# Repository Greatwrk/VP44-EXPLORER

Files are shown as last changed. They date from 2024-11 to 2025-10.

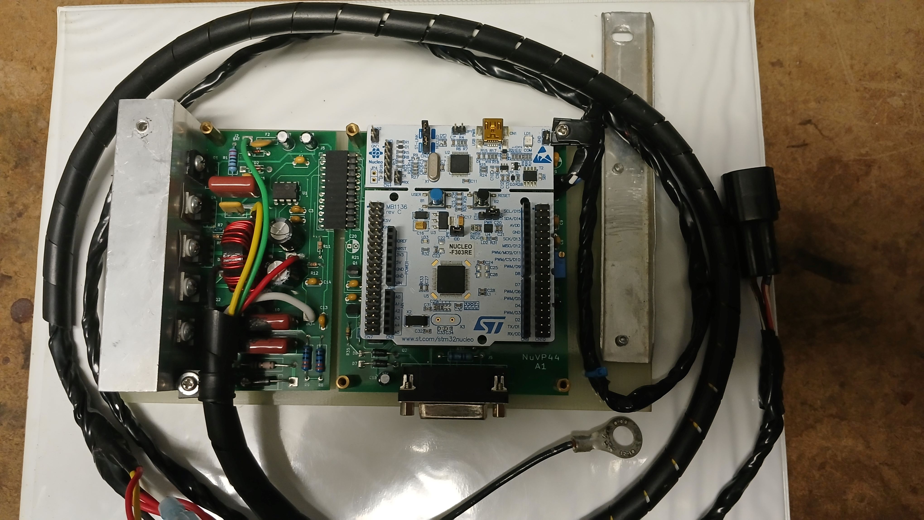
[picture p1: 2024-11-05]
images/VP44 explorer.jpg

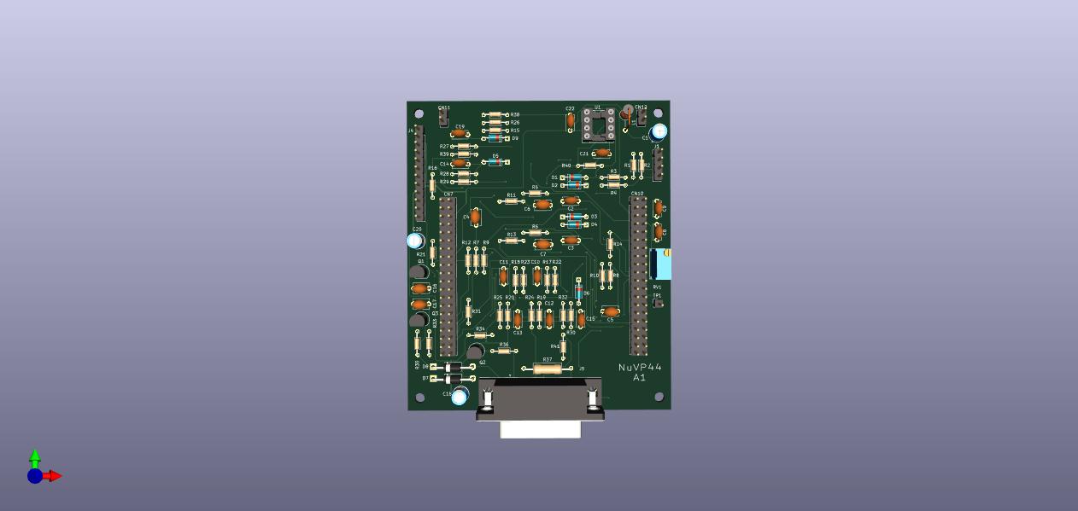
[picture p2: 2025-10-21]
vp44explorer/VP44expMainJ5/VP44expMainJ5.jpg

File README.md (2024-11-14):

# VP44 EXPLORER

My project replaces the control board that sits on top of the pump with a remote board.
The project uses an STM32f303 Nucleo dev. Board and I used Arduino IDE.
A custom PCB was made in two parts. One is the main logic and sensor interface. The second part is the 
solenoid drivers and power supply. The current driver board uses a high-speed switching buck converter
to operate the fuel solenoid. A linear drive board is under development.
The linear method is the OEM style. It generates a lot of heat and is cooled by the fuel flowing
under it in the pump housing. The switching method results in significantly less heat. The downside is the switching signal can
mask the current monitoring of the solenoid. As the armature plunger moves it causes a change in inductance which causes a small current blip.
The blip is useful to determine the solenoid dead time.

The VP44 shaft has a toothed wheel, the tooth spacing is 3 degrees of crankshaft rotation.
Every 60 degrees (120 at crankshaft) is a pair of staggered teeth.
These I refer to as the index tooth.
A dual magneto-resistive sensor with a back bias magnet senses the teeth as they pass by and creates two sinewaves.
The one that leads I refer to as phase A. The second follows by approximately 90 degrees, I refer to it as phase B.
Both signals are adaptive zero crossing detected by internal opAmps and the DACs in the STM32 and then fed to timer captures.
The software detects the index tooth region and resets a tooth edge counter to zero.
On the tooth edge 19 of the B phase the radial injection plungers are at their maximum extension.
As they follow the cam ring into compression it's at this position the injection solenoid valve must be fully transitioned to the closed position.
This is the start of injection SOI. After a variable amount of degrees, the valve de-energizes this is the end of injection EOI.

Since the solenoid has deadtime on both turn on and turn off the switching must occur before edge 19 or EOI actually happens.
This is done by computing shaft position, velocity, and acceleration to predict the relative time from a current tooth edge to edge 19.
Obviously, the closer we are to the edge 19 event the better the prediction will be, but at higher RPMs the deadtime of the solenoid results in the required prediction to
occur many degrees in advance else the valve will be closed too late or early.
That results in late injection, reduced fuel delivery and hazy smoke.
The valve must be de-energized before the moment of desired EOI because of mechanical delay I call this release time, which is about 850 microseconds.
The dead time is mostly dependent on the battery voltage and must be calculated often. 
A full current is applied to get the valve moving then the current is reduced to prevent the valve from slamming on its seat and bouncing.
Finally, the current is reduced to a safe level for the majority of the injection event.
The switch-off induction spike at EOI must be clamped at a higher voltage and low current for a fast release.
The magnetic field is determined largely by A x N turns, so keeping current low speeds the armature release.
Simple clamping / recirculating methods are too slow. A zener diode RC circuit is used. 
Some manual adjustments to times and current values must be determined with an oscilloscope and are stored.

Anyone who has kick-started or rope-started a small engine has experienced the rapid fluctuations that occur in 
crankshaft velocity. These also occur in a running engine but are greatly reduced by the flywheel mass
and inertia. These variations have to be accounted for in both the SOI time and EOI time if not the
engine will start to run rough which makes the variations worse and results in timing and delivery
errors and possible stalling or running away.

The timing advance is determined by the phase relationship of the cam ring to the crankshaft position.
The ECU decodes the crankshaft position sensor and cam sensor to create a reference signal that
occurs at 20 degrees after top dead center for each cylinder. Later engines removed the CKP and changed the camshaft gear. 
With my project, the decoding is done internally and the ECU is not required. 
The cam ring moves by a hydraulic piston which is controlled by another solenoid valve. It is PWM controlled by the MCU. 
The actual timing is calculated by the VP tooth signal phase relationship to the CKP-derived signal. 
A software servo control loop adjusts the PWM to match the computed timing with the desired timing contained in the usual look-up tables.

For now, the TPS, MAP and CKP are all that's required. The CMP is optional. A CAN interface is on the board and a CAN interface is being developed.
The Schematic and PCB were made with KiCad. The code has some low-level stuff for some of the peripherals that at the time were not supported by STM32duino.

If you build this I suggest using a 2 ohm 50 W resistor in place of the fuel solenoid for testing with a scope. The resistor can later be placed
in series with the solenoid to protect it on the bench while sweep testing at RPMs and Fuel levels. Listen for any malfunctions.
The power transistors must be isolated from the heatsink with silicon insulators. Always test isolation with an DVM.

# See it run [HERE](https://www.youtube.com/watch?v=DHwnkv7ZLJk)

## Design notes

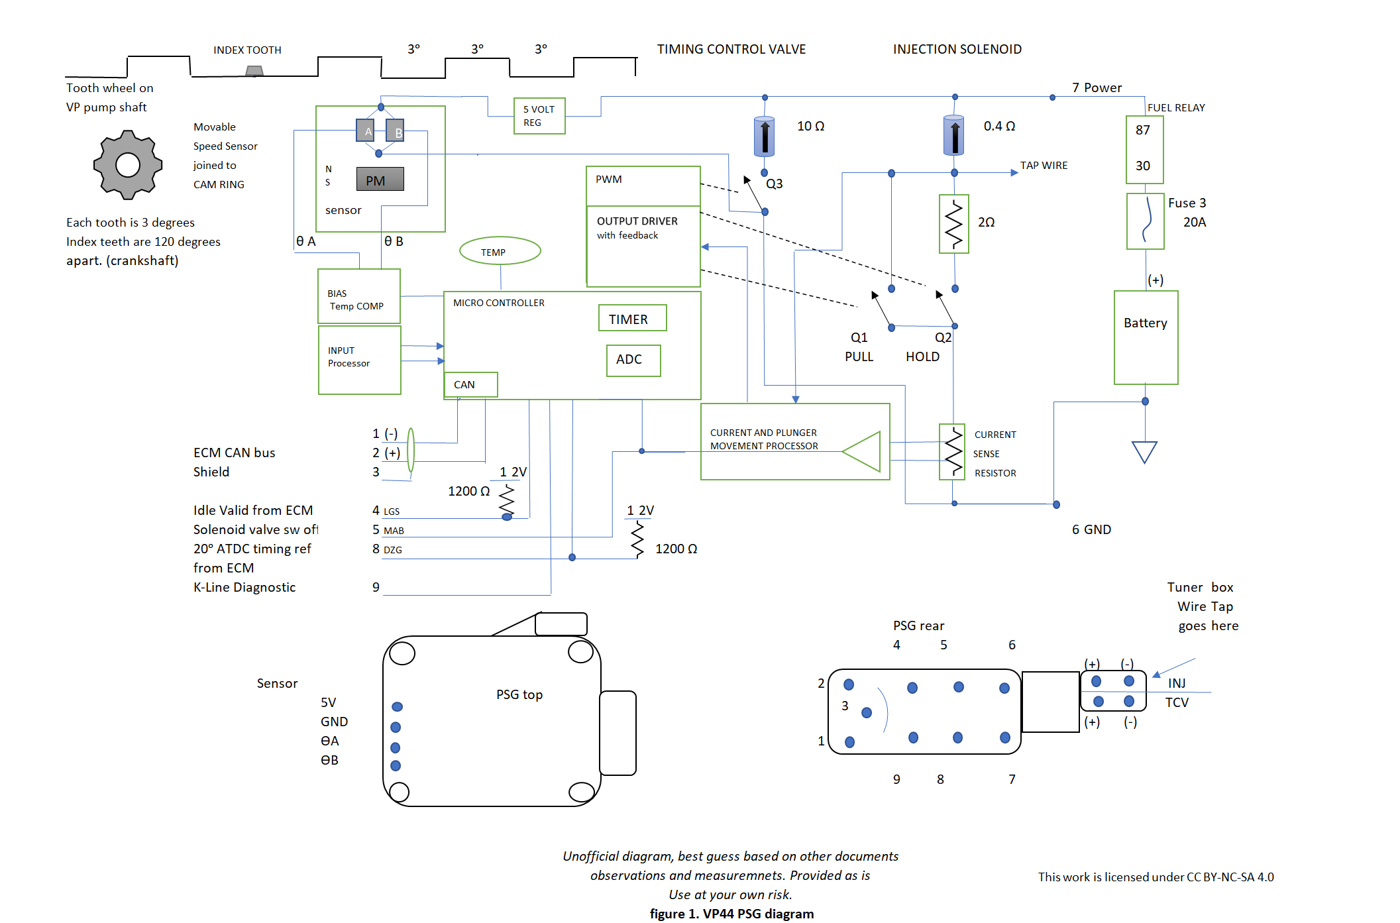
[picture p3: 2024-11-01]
images/Vp block diagram.png

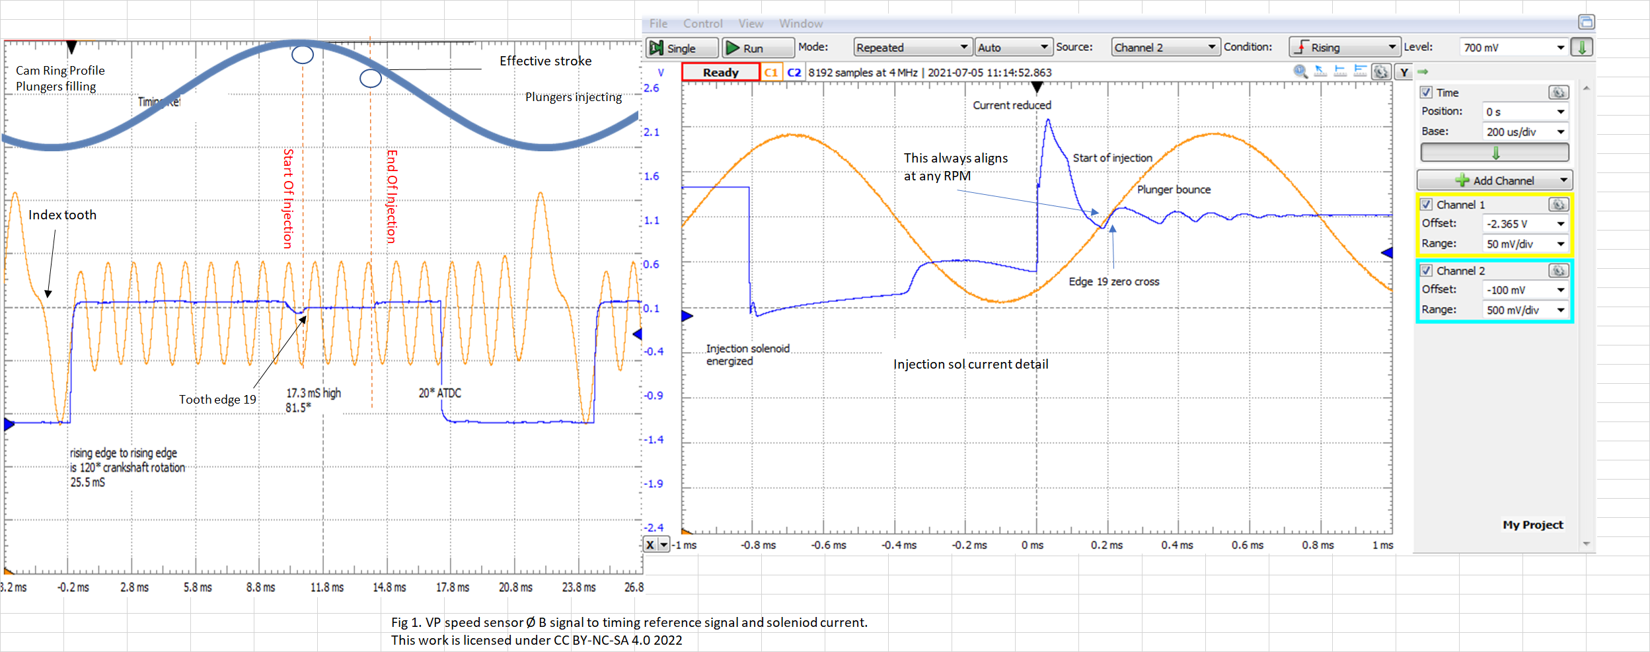
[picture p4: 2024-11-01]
images/vp roller.png

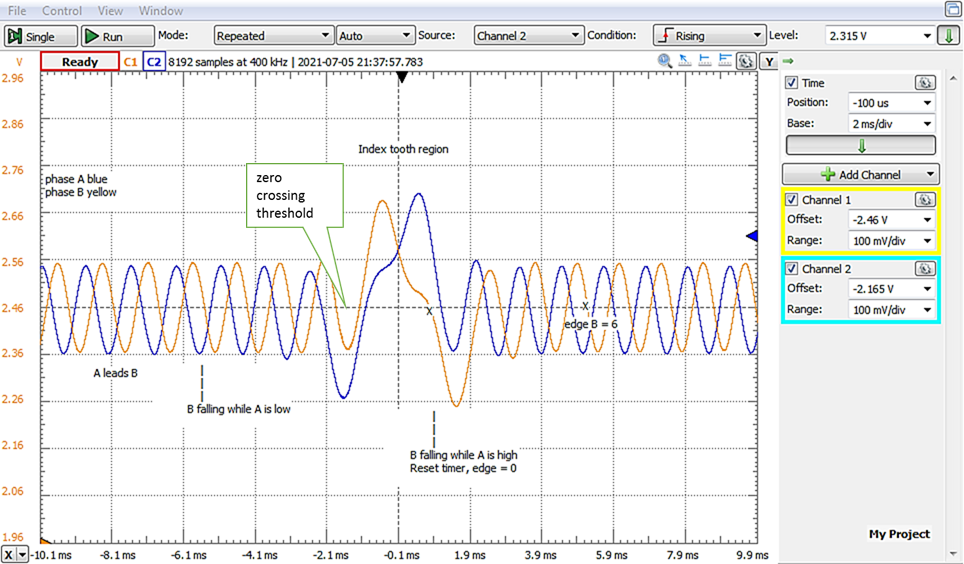
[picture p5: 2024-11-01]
images/VP44 sensor.png

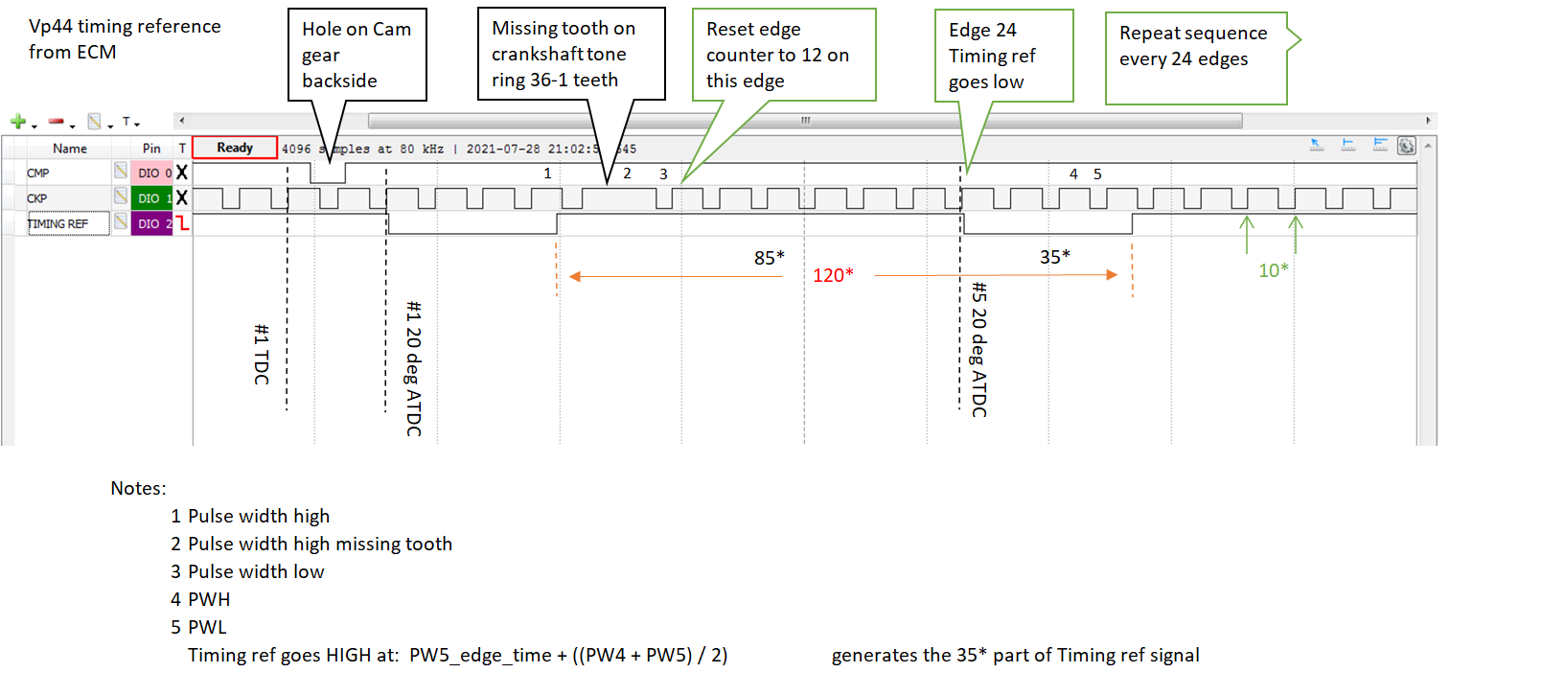
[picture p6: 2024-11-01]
images/TrefECM.png

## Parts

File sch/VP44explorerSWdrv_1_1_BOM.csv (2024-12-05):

Reference | Value | Footprint | Datasheet | Field4 | Sim.Device | Sim.Pins | Sim.Type | Qty
C1, C4, C5 | 1uF | Capacitor_THT:C_Disc_D5.1mm_W3.2mm_P5.00mm | ~ |  |  |  |  | 3
C2, C8 | 100uF | Capacitor_THT:CP_Radial_D5.0mm_P2.50mm | ~ |  |  |  |  | 2
C3, C13, C14 | 0.1uF | Capacitor_THT:C_Disc_D5.0mm_W2.5mm_P5.00mm | ~ |  |  |  |  | 3
C6, C7 | 470uF | Capacitor_THT:CP_Radial_D8.0mm_P5.00mm | ~ |  |  |  |  | 2
C9-C12 | 1uF | Capacitor_THT:C_Rect_L16.5mm_W7.0mm_P15.00mm_MKT | DigiKey EF2105-ND, MFR# ECQ-E2105KF hi quality film cap only |  |  |  |  | 4
D1 | 1N914B | Diode_THT:D_DO-35_SOD27_P7.62mm_Horizontal | ~ |  | D | 1=K 2=A |  | 1
D2 | 5.6V | Diode_THT:D_DO-41_SOD81_P10.16mm_Horizontal | ~ |  |  |  |  | 1
D3 | STPS20H100CT | Package_TO_SOT_THT:TO-220-3_Vertical | ~ |  |  |  |  | 1
D4 | 39V_5W | Diode_THT:D_DO-201AD_P15.24mm_Horizontal | ~ |  |  |  |  | 1
F1 | 20A | Automotive ATC | ~ |  |  |  |  | 1
F2 | Polyfuse 1A | Capacitor_THT:C_Disc_D8.0mm_W2.5mm_P5.00mm | MF-RHT 100-2CT-ND PTC 30V IA |  |  |  |  | 1
F3 | Polyfuse 2.5A | Capacitor_THT:C_Disc_D8.0mm_W2.5mm_P5.00mm | LITTLE FUSE POLY SWITCH 2.5A |  |  |  |  | 1
HS1 | Heatsink | 100 X 40 X20 AMAZON.COM | ~ |  |  |  |  | 1
J1 | GND | Connector_Wire:SolderWire-2sqmm_1x01_D2mm_OD3.9mm | ~ |  |  |  |  | 1
J2 | BAT | Connector_Wire:SolderWire-2sqmm_1x01_D2mm_OD3.9mm | ~ |  |  |  |  | 1
J3 | TCV | Connector_Wire:SolderWire-2sqmm_1x01_D2mm_OD3.9mm | ~ |  |  |  |  | 1
J4 | INJ+ | Connector_Wire:SolderWire-2sqmm_1x01_D2mm_OD3.9mm | ~ |  |  |  |  | 1
J5 | Conn_01x12 | Connector_PinHeader_2.54mm:PinHeader_1x12_P2.54mm_Right angle female | ~ S5448-ND |  |  |  |  | 1
J6 | INJ | Connector_Wire:SolderWire-2sqmm_1x01_D2mm_OD3.9mm | ~ | INJ- |  |  |  | 1
L1 | L_Ferrite | Inductor_THT:L_Toroid_Vertical_L26.7mm_W14.0mm_P10.16mm_Pulse_D | Amazon.com DC 300W 20A step down buck converter, re used coil |  |  |  |  | 1
L2 | TCV_SOL |  | ~ |  |  |  |  | 1
L3 | INJ_SOL |  | ~ |  |  |  |  | 1
Q1 | MJF44H11G | Package_TO_SOT_THT:TO-220-3_Vertical | https://www.onsemi.com/pub/Collateral/BDW93C-D.pdf |  |  |  |  | 1
Q2 | IRF135B203 | Package_TO_SOT_THT:TO-220-3_Vertical | https://www.st.com/resource/en/datasheet/stp40n60m2.pdf |  | NMOS | 1=D 2=G 3=S | VDMOS | 1
Q3, Q4 | STP40NF10L | Package_TO_SOT_THT:TO-220-3_Vertical | https://www.st.com/resource/en/datasheet/stp40n60m2.pdf |  | NMOS | 1=D 2=G 3=S | VDMOS | 2
R1 | 220R | Resistor_THT:R_Axial_DIN0309_L9.0mm_D3.2mm_P15.24mm_Horizontal | ~ |  |  |  |  | 1
R2, R4 | 27R | Resistor_THT:R_Axial_DIN0204_L3.6mm_D1.6mm_P7.62mm_Horizontal | ~ |  |  |  |  | 2
R3, R5, R8, R11-R14 | 10K | Resistor_THT:R_Axial_DIN0204_L3.6mm_D1.6mm_P7.62mm_Horizontal | ~ |  |  |  |  | 7
R6, R9 | 330R | Resistor_THT:R_Axial_DIN0309_L9.0mm_D3.2mm_P15.24mm_Horizontal | ~ |  |  |  |  | 2
R7 | 100R | Resistor_THT:R_Axial_DIN0204_L3.6mm_D1.6mm_P7.62mm_Horizontal | ~ |  |  |  |  | 1
R10 | 1R_1W | Resistor_THT:R_Axial_DIN0414_L11.9mm_D4.5mm_P20.32mm_Horizontal | ~ |  |  |  |  | 1
U1 | MCP14E7 | Package_DIP:DIP-8_W7.62mm | http://ww1.microchip.com/downloads/en/DeviceDoc/MCP14E7.pdf |  |  |  |  | 1
U2 | ACS712xLCTR-20A | Package_SO:SOIC-8_3.9x4.9mm_P1.27mm | http://www.allegromicro.com/~/media/Files/Datasheets/ACS712-Datasheet.ashx?la=en |  |  |  |  | 1

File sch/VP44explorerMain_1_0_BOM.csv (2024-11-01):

Reference | Value | Footprint | Datasheet | Qty
C1, C18, C20 | 100uF | Capacitor_THT:CP_Radial_D5.0mm_P2.50mm | ~ | 3
C2, C3 | 4.7nF | Capacitor_THT:C_Disc_D5.0mm_W2.5mm_P5.00mm | ~ | 2
C4-C7, C16, C17 | 1uF | Capacitor_THT:C_Disc_D5.1mm_W3.2mm_P5.00mm | ~ | 6
C8, C12, C13 | 300pF | Capacitor_THT:C_Disc_D5.0mm_W2.5mm_P5.00mm | ~ | 3
C9, C19 | 10nF | Capacitor_THT:C_Disc_D5.0mm_W2.5mm_P5.00mm | ~ | 2
C10, C11, C14, C15, C21, C22 | 0.1uF | Capacitor_THT:C_Disc_D5.0mm_W2.5mm_P5.00mm | ~ | 6
CN7, CN10 | Conn_02x20_Odd_Even | Connector_PinHeader_2.54mm:PinHeader_2x20_P2.54mm_Vertical | ~ | 2
CN11, CN12 | Conn_01x02_Female | Connector_PinHeader_2.54mm:PinHeader_1x02_P2.54mm_Vertical | ~ | 2
D1-D6, D9 | 1N914B | Diode_THT:D_DO-35_SOD27_P7.62mm_Horizontal | ~ | 7
D7, D8 | 1N5393 | Diode_THT:D_DO-41_SOD81_P12.70mm_Horizontal | ~ | 2
J1 | Conn_01x04_Shielded | Connector_PinHeader_2.54mm:PinHeader_1x04_P2.54mm_Vertical | ~ | 1
J4 | Conn_01x12 | Connector_PinHeader_2.54mm:PinHeader_1x12_P2.54mm_Vertical | ~ | 1
J5 | DB15_Male_MountingHoles | Connector_Dsub:DSUB-15_Male_Horizontal_P2.77x2.84mm_EdgePinOffset4.94mm_Housed_MountingHolesOffset7.48mm | digikey 182-15FE-ND , MFR 182-015-213R531 | 1
L1 | 500uH | Inductor_THT:L_Axial_L11.0mm_D4.5mm_P5.08mm_Vertical_Fastron_MECC | ~ | 1
Q1, Q2 | PN2222A | Package_TO_SOT_THT:TO-92_Inline | http://www.fairchildsemi.com/ds/PN/PN2222A.pdf | 2
Q3 | BC327 | Package_TO_SOT_THT:TO-92_Inline | http://www.onsemi.com/pub_link/Collateral/BC327-D.PDF | 1
R1-R4, R7, R8, R31, R41 | 1.5K | Resistor_THT:R_Axial_DIN0204_L3.6mm_D1.6mm_P7.62mm_Horizontal | ~ | 8
R5, R6, R26 | 47K | Resistor_THT:R_Axial_DIN0204_L3.6mm_D1.6mm_P7.62mm_Horizontal | ~ | 3
R9, R10 | 470K | Resistor_THT:R_Axial_DIN0204_L3.6mm_D1.6mm_P7.62mm_Horizontal | ~ | 2
R11, R13, R15 | 1K | Resistor_THT:R_Axial_DIN0204_L3.6mm_D1.6mm_P7.62mm_Horizontal | ~ | 3
R12, R14, R17-R20, R22-R25, R30, R32, R34, R39 | 10K | Resistor_THT:R_Axial_DIN0204_L3.6mm_D1.6mm_P7.62mm_Horizontal | ~ | 14
R16, R27, R33 | 4.7K | Resistor_THT:R_Axial_DIN0204_L3.6mm_D1.6mm_P7.62mm_Horizontal | ~ | 3
R21 | 2.2K | Resistor_THT:R_Axial_DIN0204_L3.6mm_D1.6mm_P7.62mm_Horizontal | ~ | 1
R28 | 3.9K | Resistor_THT:R_Axial_DIN0204_L3.6mm_D1.6mm_P7.62mm_Horizontal | ~ | 1
R29 | 15K | Resistor_THT:R_Axial_DIN0204_L3.6mm_D1.6mm_P7.62mm_Horizontal | ~ | 1
R35 | 100K | Resistor_THT:R_Axial_DIN0204_L3.6mm_D1.6mm_P7.62mm_Horizontal | ~ | 1
R36 | 33R | Resistor_THT:R_Axial_DIN0204_L3.6mm_D1.6mm_P7.62mm_Horizontal | ~ | 1
R37 | 4.7R_1/2W | Resistor_THT:R_Axial_DIN0309_L9.0mm_D3.2mm_P15.24mm_Horizontal | ~ | 1
R38 | 2K | Resistor_THT:R_Axial_DIN0204_L3.6mm_D1.6mm_P7.62mm_Horizontal | ~ | 1
R40 | 120R | Resistor_THT:R_Axial_DIN0204_L3.6mm_D1.6mm_P7.62mm_Horizontal | ~ | 1
RV1 | 100K | Potentiometer_THT:Potentiometer_Bourns_3296W_Vertical | ~ | 1
TP1 | Conn_01x01_Male | Connector_PinHeader_2.54mm:PinHeader_1x01_P2.54mm_Vertical | ~ | 1
U1 | MCP2562-E-P | Package_DIP:DIP-8_W7.62mm_Socket | http://ww1.microchip.com/downloads/en/DeviceDoc/25167A.pdf | 1

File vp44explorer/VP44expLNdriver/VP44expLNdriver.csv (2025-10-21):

Source: | C:\Users\Marcus\Desktop\PCroll\032523nudrvsw\041723nudrln\041723nudrln.kicad_sch
Date: | 4/29/2023 2:43:34 PM
Tool: | Eeschema (7.0.0)
Generator: | C:\Program Files\KiCad\7.0\bin\scripting\plugins/bom_csv_grouped_by_value_with_fp.py
Component Count: | 43
Ref | Qnty | Value | Cmp name | Footprint | Description | Vendor | DNP
C1, C4 | 2 | 1uF | C | Capacitor_THT:C_Disc_D5.1mm_W3.2mm_P5.00mm | Unpolarized capacitor
C2, C6 | 2 | 0.1uF | C | Capacitor_THT:C_Disc_D5.1mm_W3.2mm_P5.00mm | Unpolarized capacitor
C3, C7 | 2 | 100uF | C_Polarized_US | Capacitor_THT:CP_Radial_D5.0mm_P2.50mm | Polarized capacitor, US symbol
C5 | 1 | 100pF | C | Capacitor_THT:C_Disc_D5.1mm_W3.2mm_P5.00mm | Unpolarized capacitor
C8 | 1 | 1uF | C | Capacitor_THT:C_Rect_L16.5mm_W7.0mm_P15.00mm_MKT | Unpolarized capacitor
C9 | 1 | 0.1uF | C | Capacitor_THT:C_Rect_L16.5mm_W7.0mm_P15.00mm_MKT | Unpolarized capacitor
D1 | 1 | 1N914B | D | Diode_THT:D_DO-35_SOD27_P7.62mm_Horizontal | Diode
D2 | 1 | 5.6V | D_Zener | Diode_THT:D_DO-41_SOD81_P10.16mm_Horizontal | Zener diode
D3, D4 | 2 | 31V | D_Zener | MYfootprints:D_DO-201AD_P17.78mm_Horizontal | Zener diode
F2, F3 | 2 | Polyfuse | Polyfuse | Capacitor_THT:C_Disc_D8.0mm_W2.5mm_P5.00mm | Resettable fuse, polymeric positive temperature coefficient
J1 | 1 | GND | Conn_01x01_Pin_3 | Connector_Wire:SolderWire-2sqmm_1x01_D2mm_OD3.9mm | Generic connector, single row, 01x01, script generated
J2 | 1 | BAT+ | Conn_01x01_Pin_4 | Connector_Wire:SolderWire-2sqmm_1x01_D2mm_OD3.9mm | Generic connector, single row, 01x01, script generated
J3 | 1 | Conn_01x12 | Conn_01x12 | Connector_PinHeader_2.54mm:PinHeader_1x12_P2.54mm_Vertical | Generic connector, single row, 01x12, script generated (kicad-library-utils/schlib/autogen/connector/)
J4 | 1 | INJ- | Conn_01x01_Pin_1 | Connector_Wire:SolderWire-2sqmm_1x01_D2mm_OD3.9mm | Generic connector, single row, 01x01, script generated
J5 | 1 | TCV- | Conn_01x01_Pin_2 | Connector_Wire:SolderWire-2sqmm_1x01_D2mm_OD3.9mm | Generic connector, single row, 01x01, script generated
J6, J7 | 2 | TCV | Conn_01x01_Pin_2 | Connector_Wire:SolderWire-0.5sqmm_1x01_D0.9mm_OD2.1mm | Generic connector, single row, 01x01, script generated
Q1 | 1 | MJF44H11G | MJE13003 | Package_TO_SOT_THT:TO-220-3_Vertical | 1.5A Ic, 400V Vce, Silicon Switching Power NPN Transistor, TO-225
Q2 | 1 | IRF250P225 | STB40N60M2 | Package_TO_SOT_THT:TO-247-3_Vertical | 34A Id, 600V Vds, N-Channel MDmesh M2 MOSFET, 78mOhm Ron, D2PAK
Q3 | 1 | IRL2910 | STB40N60M2 | Package_TO_SOT_THT:TO-220-3_Vertical | 34A Id, 600V Vds, N-Channel MDmesh M2 MOSFET, 78mOhm Ron, D2PAK
Q4 | 1 | 75NF20 | STB40N60M2 | Package_TO_SOT_THT:TO-220-3_Vertical | 34A Id, 600V Vds, N-Channel MDmesh M2 MOSFET, 78mOhm Ron, D2PAK
R1, R3, R4, R5, R6, R7, R11, R12 | 8 | 10K | R | Resistor_THT:R_Axial_DIN0204_L3.6mm_D1.6mm_P7.62mm_Horizontal | Resistor
R2, R16 | 2 | 220R | R | Resistor_THT:R_Axial_DIN0309_L9.0mm_D3.2mm_P15.24mm_Horizontal | Resistor
R8 | 1 | .05R | R | Resistor_THT:R_Axial_DIN0516_L15.5mm_D5.0mm_P25.40mm_Horizontal | Resistor
R9, R13 | 2 | 100R | R | Resistor_THT:R_Axial_DIN0204_L3.6mm_D1.6mm_P5.08mm_Horizontal | Resistor
R10 | 1 | 100R | R | Resistor_THT:R_Axial_DIN0204_L3.6mm_D1.6mm_P7.62mm_Horizontal | Resistor
R14, R15 | 2 | 1R | R | Package_TO_SOT_THT:TO-220-2_Vertical | Resistor
U1 | 1 | Opamp_Quad | Opamp_Quad | Package_DIP:DIP-14_W7.62mm_Socket | Quad operational amplifier

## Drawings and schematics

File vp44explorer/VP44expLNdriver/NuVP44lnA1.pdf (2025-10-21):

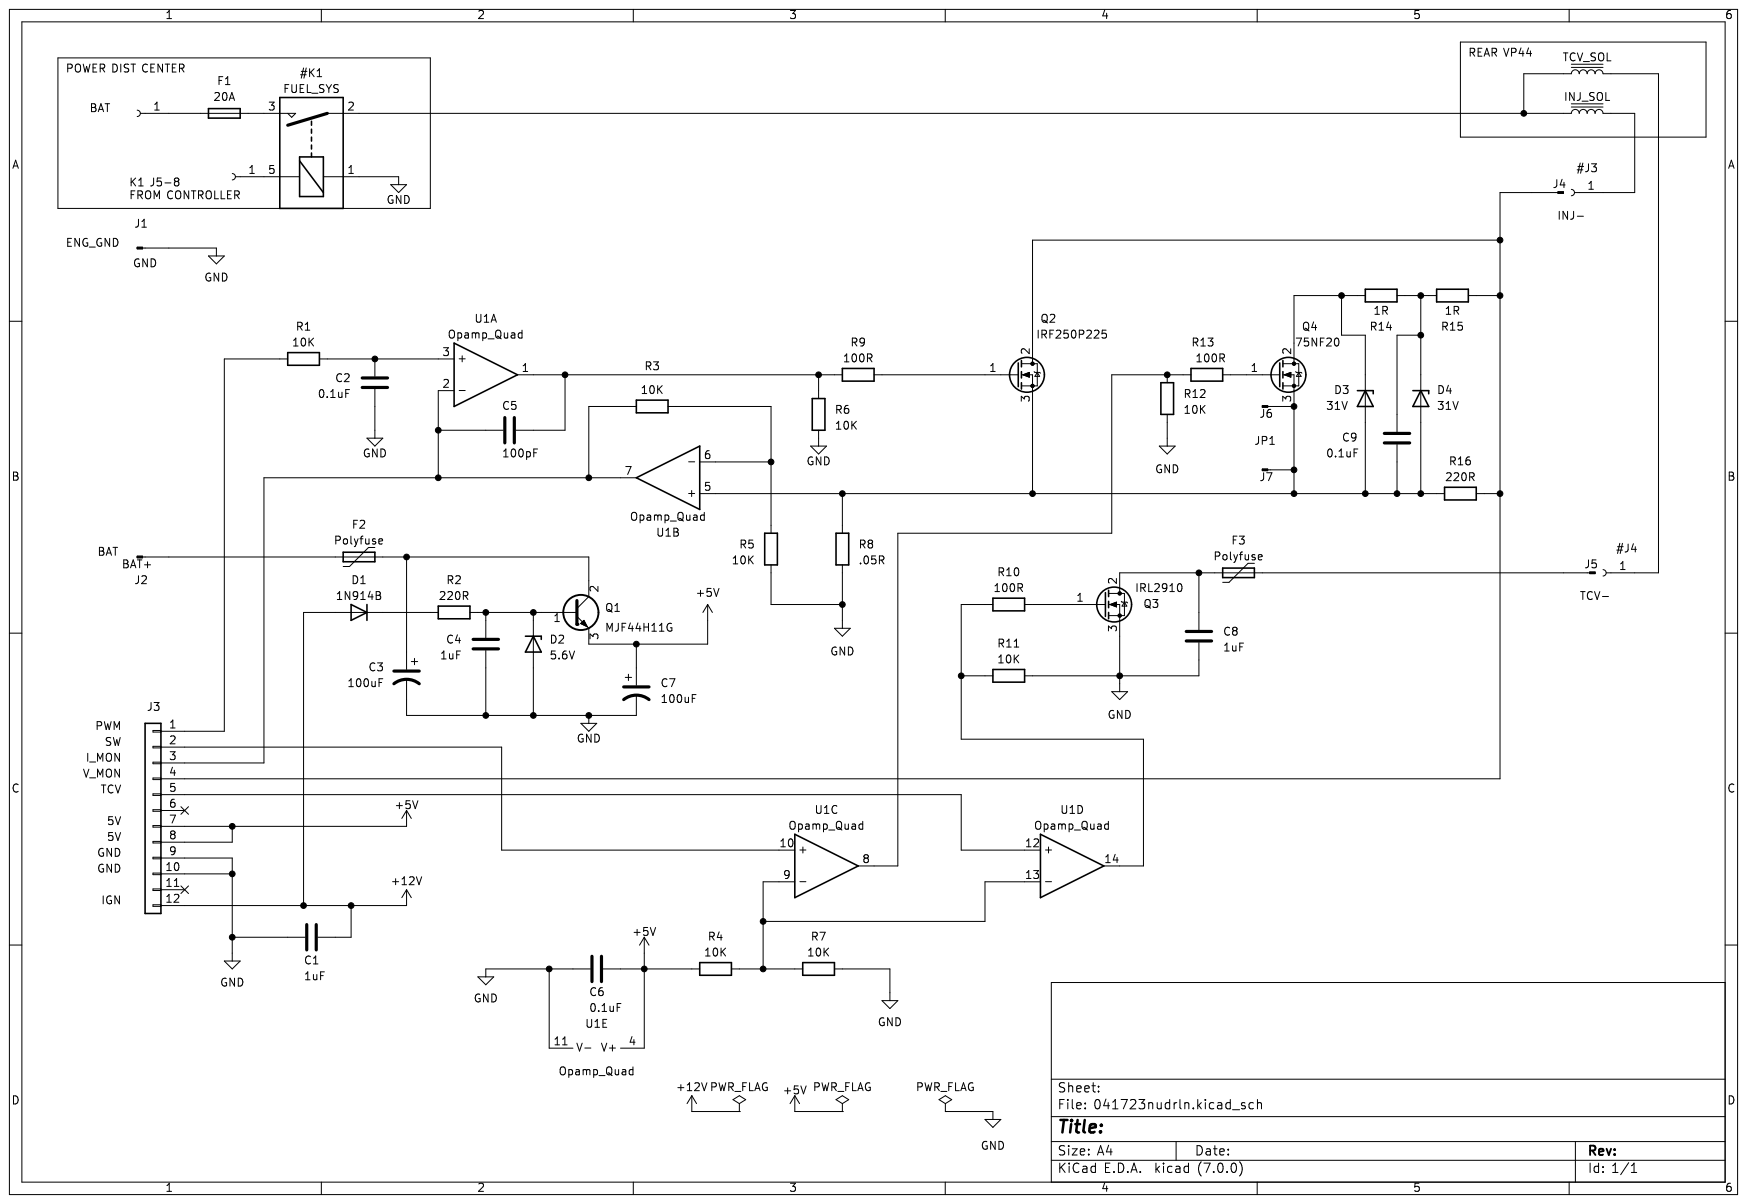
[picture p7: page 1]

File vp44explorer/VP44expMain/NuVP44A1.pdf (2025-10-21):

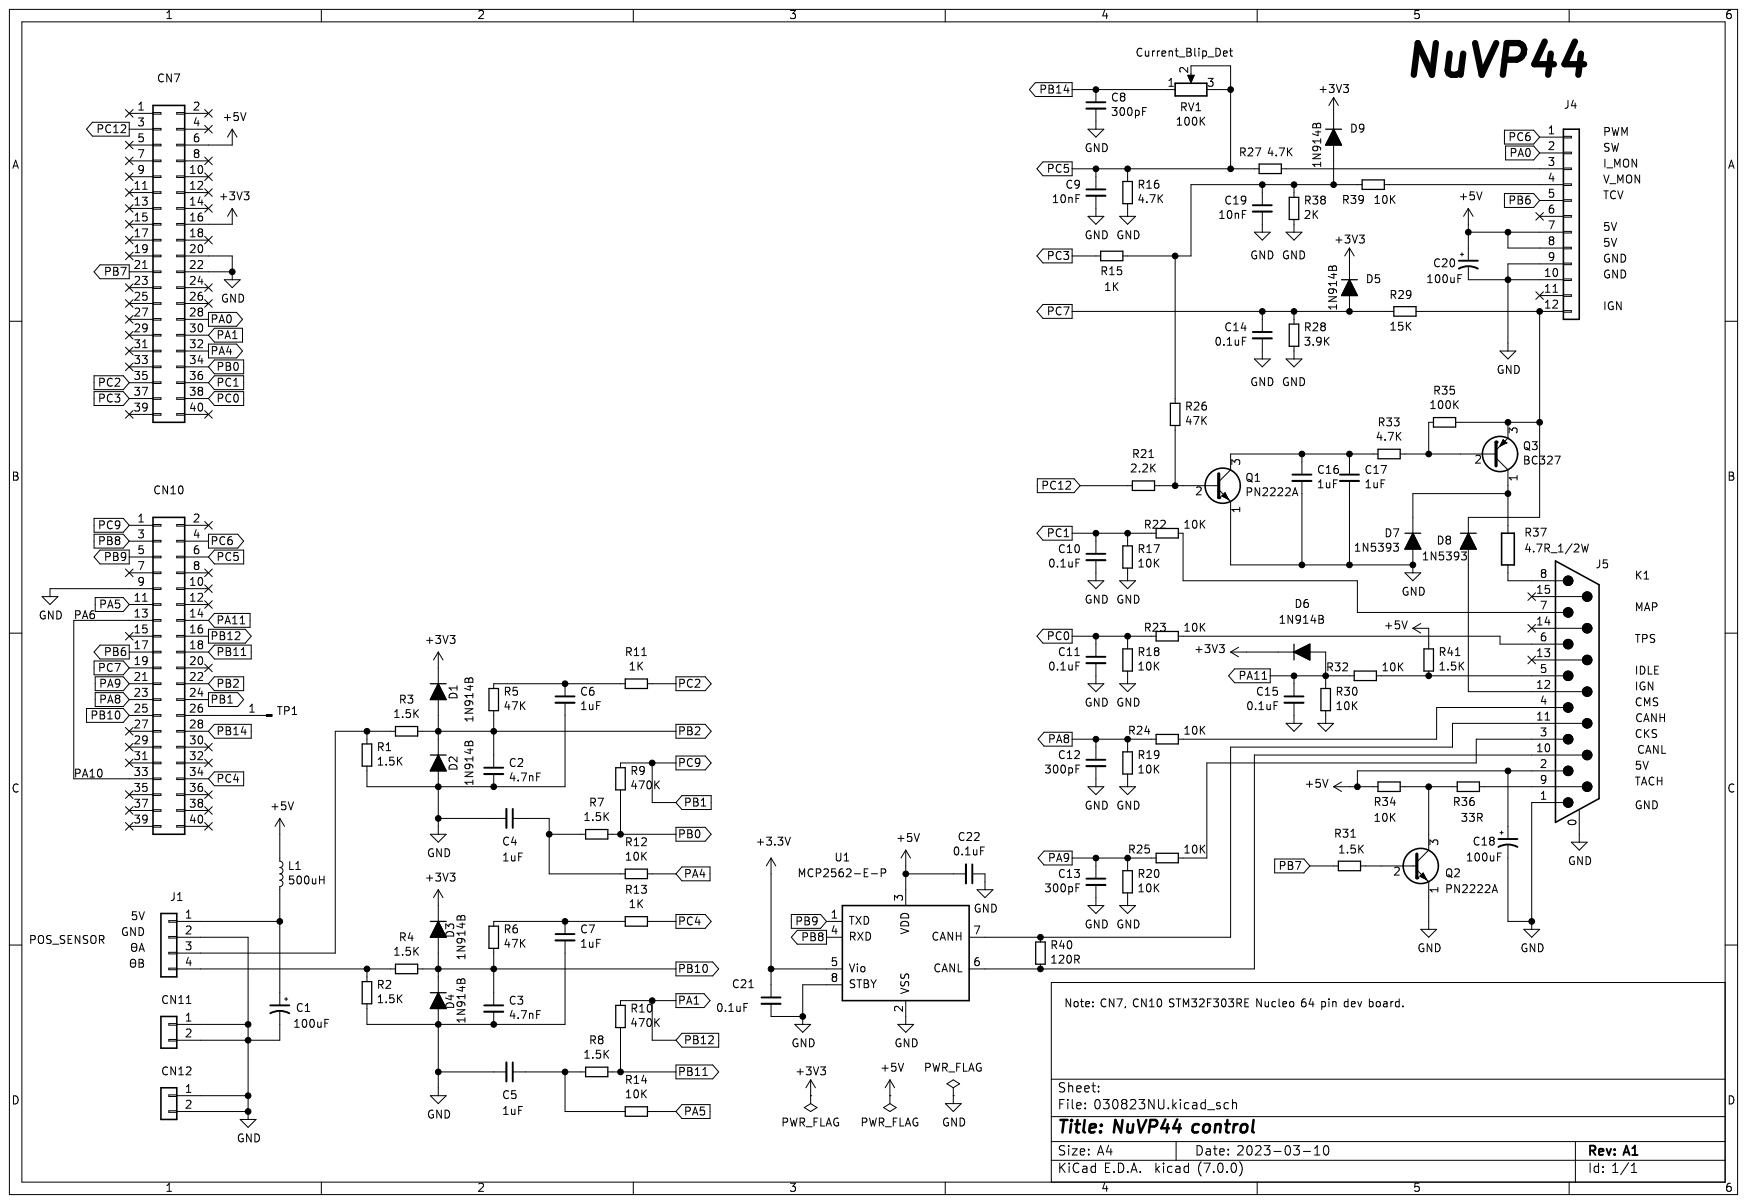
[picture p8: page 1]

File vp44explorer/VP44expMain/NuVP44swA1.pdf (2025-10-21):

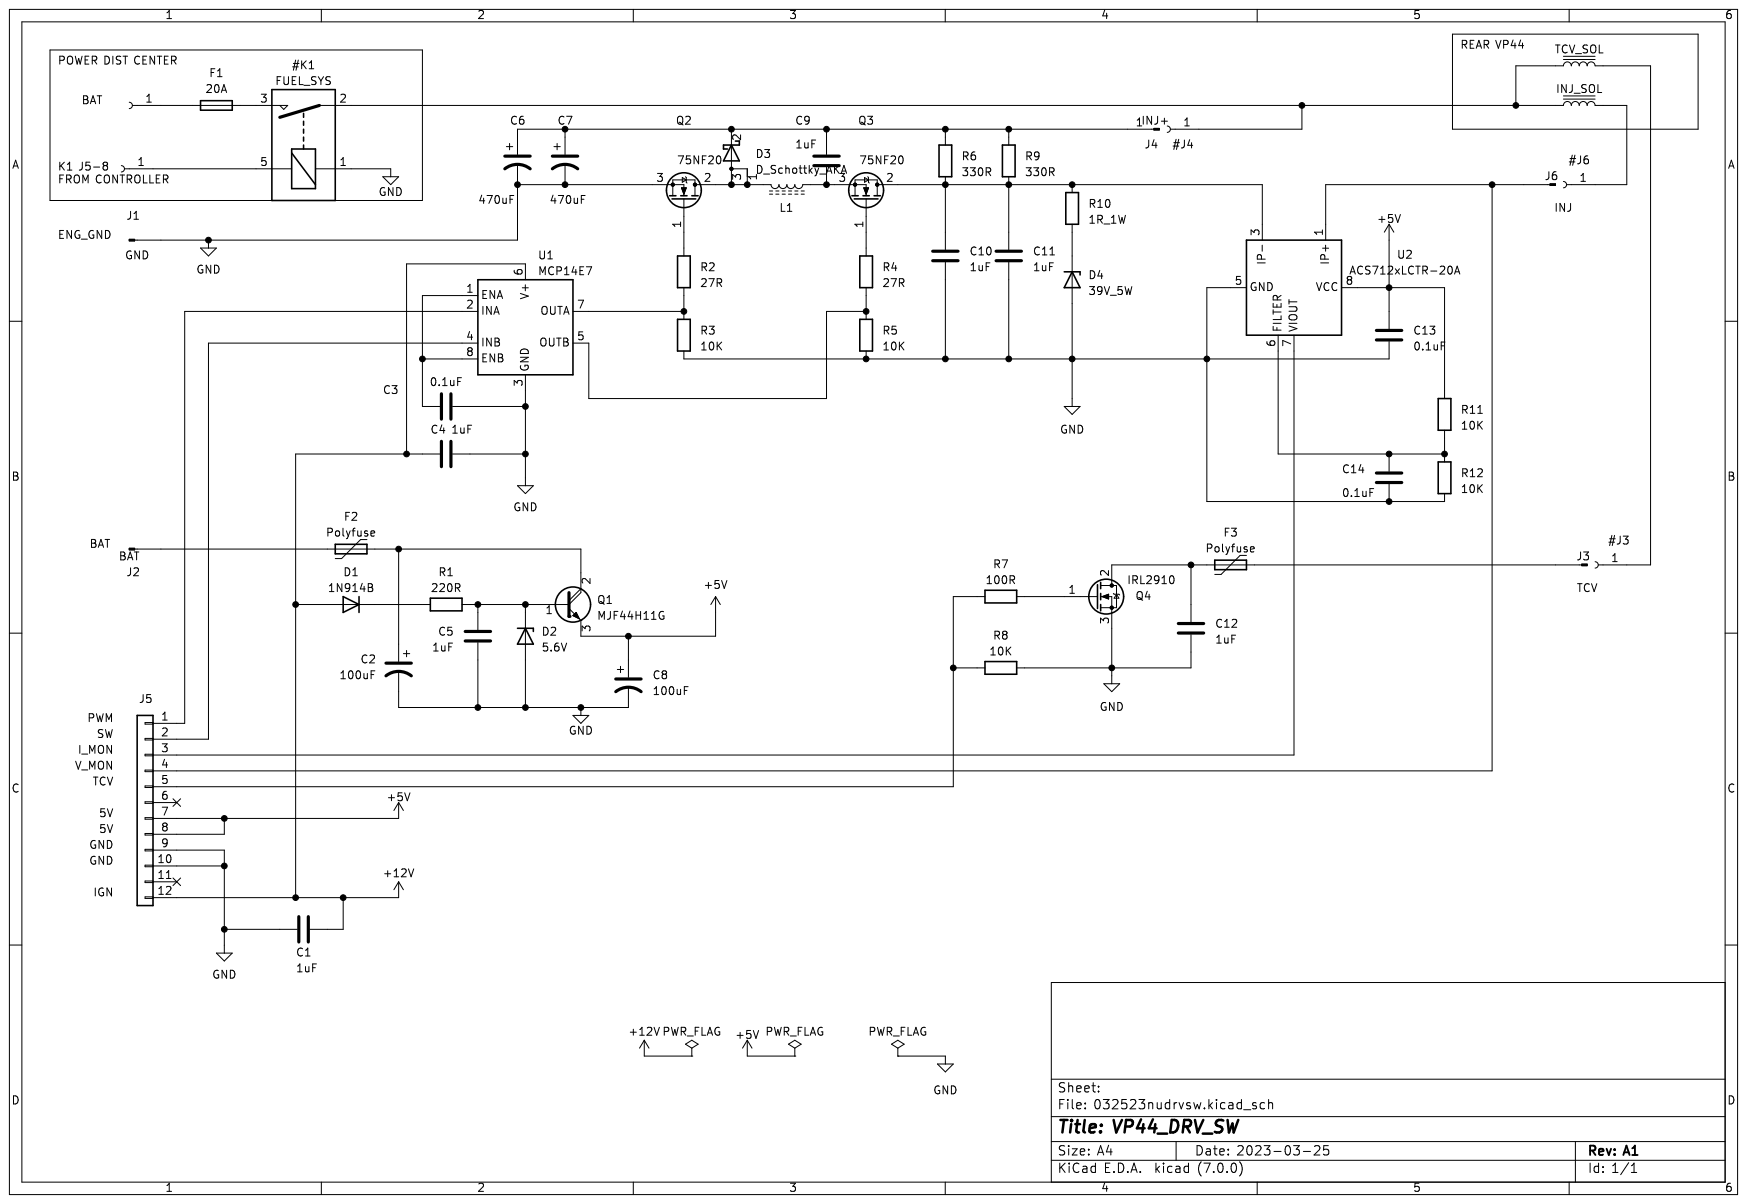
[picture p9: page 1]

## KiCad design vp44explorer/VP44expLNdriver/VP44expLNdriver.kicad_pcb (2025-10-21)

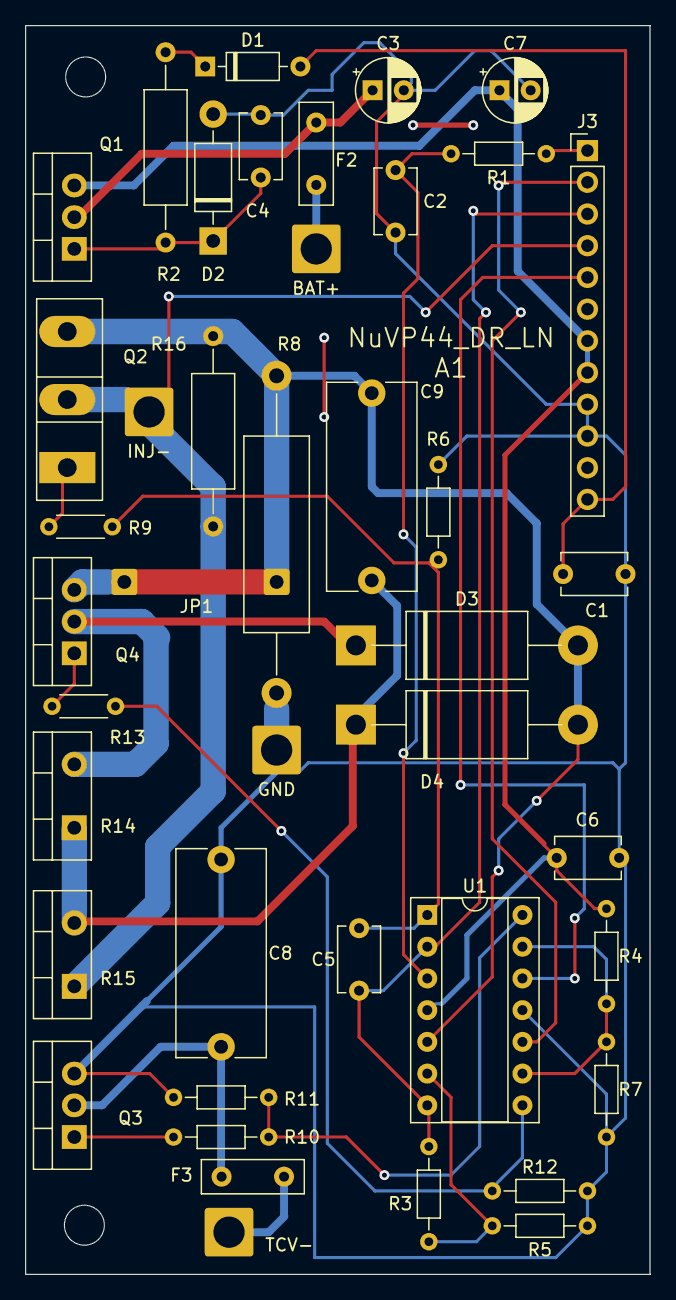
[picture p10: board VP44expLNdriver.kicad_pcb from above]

Board: 2 copper layers, 50.0 x 100.0 mm, 45 parts (0 on the bottom side), 26 nets.

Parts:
C1, C4: 1uF; C_Disc_D5.1mm_W3.2mm_P5.00mm
C2, C6: 0.1uF; C_Disc_D5.1mm_W3.2mm_P5.00mm
C3, C7: 100uF; CP_Radial_D5.0mm_P2.50mm
C5: 100pF; C_Disc_D5.1mm_W3.2mm_P5.00mm
C8: 1uF; C_Rect_L16.5mm_W7.0mm_P15.00mm_MKT
C9: 0.1uF; C_Rect_L16.5mm_W7.0mm_P15.00mm_MKT
D1: 1N914B; D_DO-35_SOD27_P7.62mm_Horizontal
D2: 5.6V; D_DO-41_SOD81_P10.16mm_Horizontal
D3, D4: 31V; D_DO-201AD_P17.78mm_Horizontal
F2, F3: Polyfuse; C_Disc_D8.0mm_W2.5mm_P5.00mm
J1: GND; SolderWire-2sqmm_1x01_D2mm_OD3.9mm
J2: BAT+; SolderWire-2sqmm_1x01_D2mm_OD3.9mm
J3: Conn_01x12; PinHeader_1x12_P2.54mm_Vertical
J4: INJ-; SolderWire-2sqmm_1x01_D2mm_OD3.9mm
J5: TCV-; SolderWire-2sqmm_1x01_D2mm_OD3.9mm
J6, J7: TCV; SolderWire-0.5sqmm_1x01_D0.9mm_OD2.1mm
MH1, MH2: MountingHole_3.2mm_M3
Q1: MJF44H11G; TO-220-3_Vertical
Q2: IRF250P225; TO-247-3_Vertical
Q3: IRL2910; TO-220-3_Vertical
Q4: 75NF20; TO-220-3_Vertical
R1, R3, R4, R5, R6, R7, R11, R12: 10K; R_Axial_DIN0204_L3.6mm_D1.6mm_P7.62mm_Horizontal
R2, R16: 220R; R_Axial_DIN0309_L9.0mm_D3.2mm_P15.24mm_Horizontal
R8: .05R; R_Axial_DIN0516_L15.5mm_D5.0mm_P25.40mm_Horizontal
R9, R13: 100R; R_Axial_DIN0204_L3.6mm_D1.6mm_P5.08mm_Horizontal
R10: 100R; R_Axial_DIN0204_L3.6mm_D1.6mm_P7.62mm_Horizontal
R14, R15: 1R; TO-220-2_Vertical
U1: Opamp_Quad; DIP-14_W7.62mm_Socket

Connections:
+5V: C6.2, C7.1, J3.7, J3.8, Q1.3 (E), R4.1, U1.4 (V+)
+12V: C1.2, D1.2 (A), J3.12
GND: C1.1, C2.1, C3.2, C4.1, C6.1, C7.2, C8.1, D2.2 (A), J1.1, J3.9, J3.10, Q3.3 (S), R5.1, R6.2, R7.2, R8.2, R11.2, R12.2, U1.11 (V-)
unnamed: C5.2, R6.1, R9.1, U1.1
unnamed: D1.1 (K), R2.1
unnamed: C4.2, D2.1 (K), Q1.1 (B), R2.2
unnamed: C9.1, D3.2 (A), D4.2 (A), J6.1, J7.1, Q2.3 (S), Q4.3 (S), R8.1, R16.1, U1.5 (+)
unnamed: D3.1 (K), Q4.2 (D), R14.2
unnamed: C9.2, D4.1 (K), R14.1, R15.2
unnamed: F2.1, J2.1
unnamed: J3.1, R1.1
unnamed: J3.2, U1.10 (+)
unnamed: C5.1, J3.3, R3.1, U1.2 (-), U1.7
unnamed: J3.4, J4.1, Q2.2 (D), R15.1, R16.2
unnamed: J3.5, U1.12 (+)
unnamed: F3.2, J5.1
unnamed: C3.1, F2.2, Q1.2 (C)
unnamed: Q2.1 (G), R9.2
unnamed: C8.2, F3.1, Q3.2 (D)
unnamed: Q3.1 (G), R10.2
unnamed: Q4.1 (G), R13.1
unnamed: R10.1, R11.1, U1.14
unnamed: R12.1, R13.2, U1.8
unnamed: C2.2, R1.2, U1.3 (+)
unnamed: R3.2, R5.2, U1.6 (-)
unnamed: R4.2, R7.1, U1.9 (-), U1.13 (-)

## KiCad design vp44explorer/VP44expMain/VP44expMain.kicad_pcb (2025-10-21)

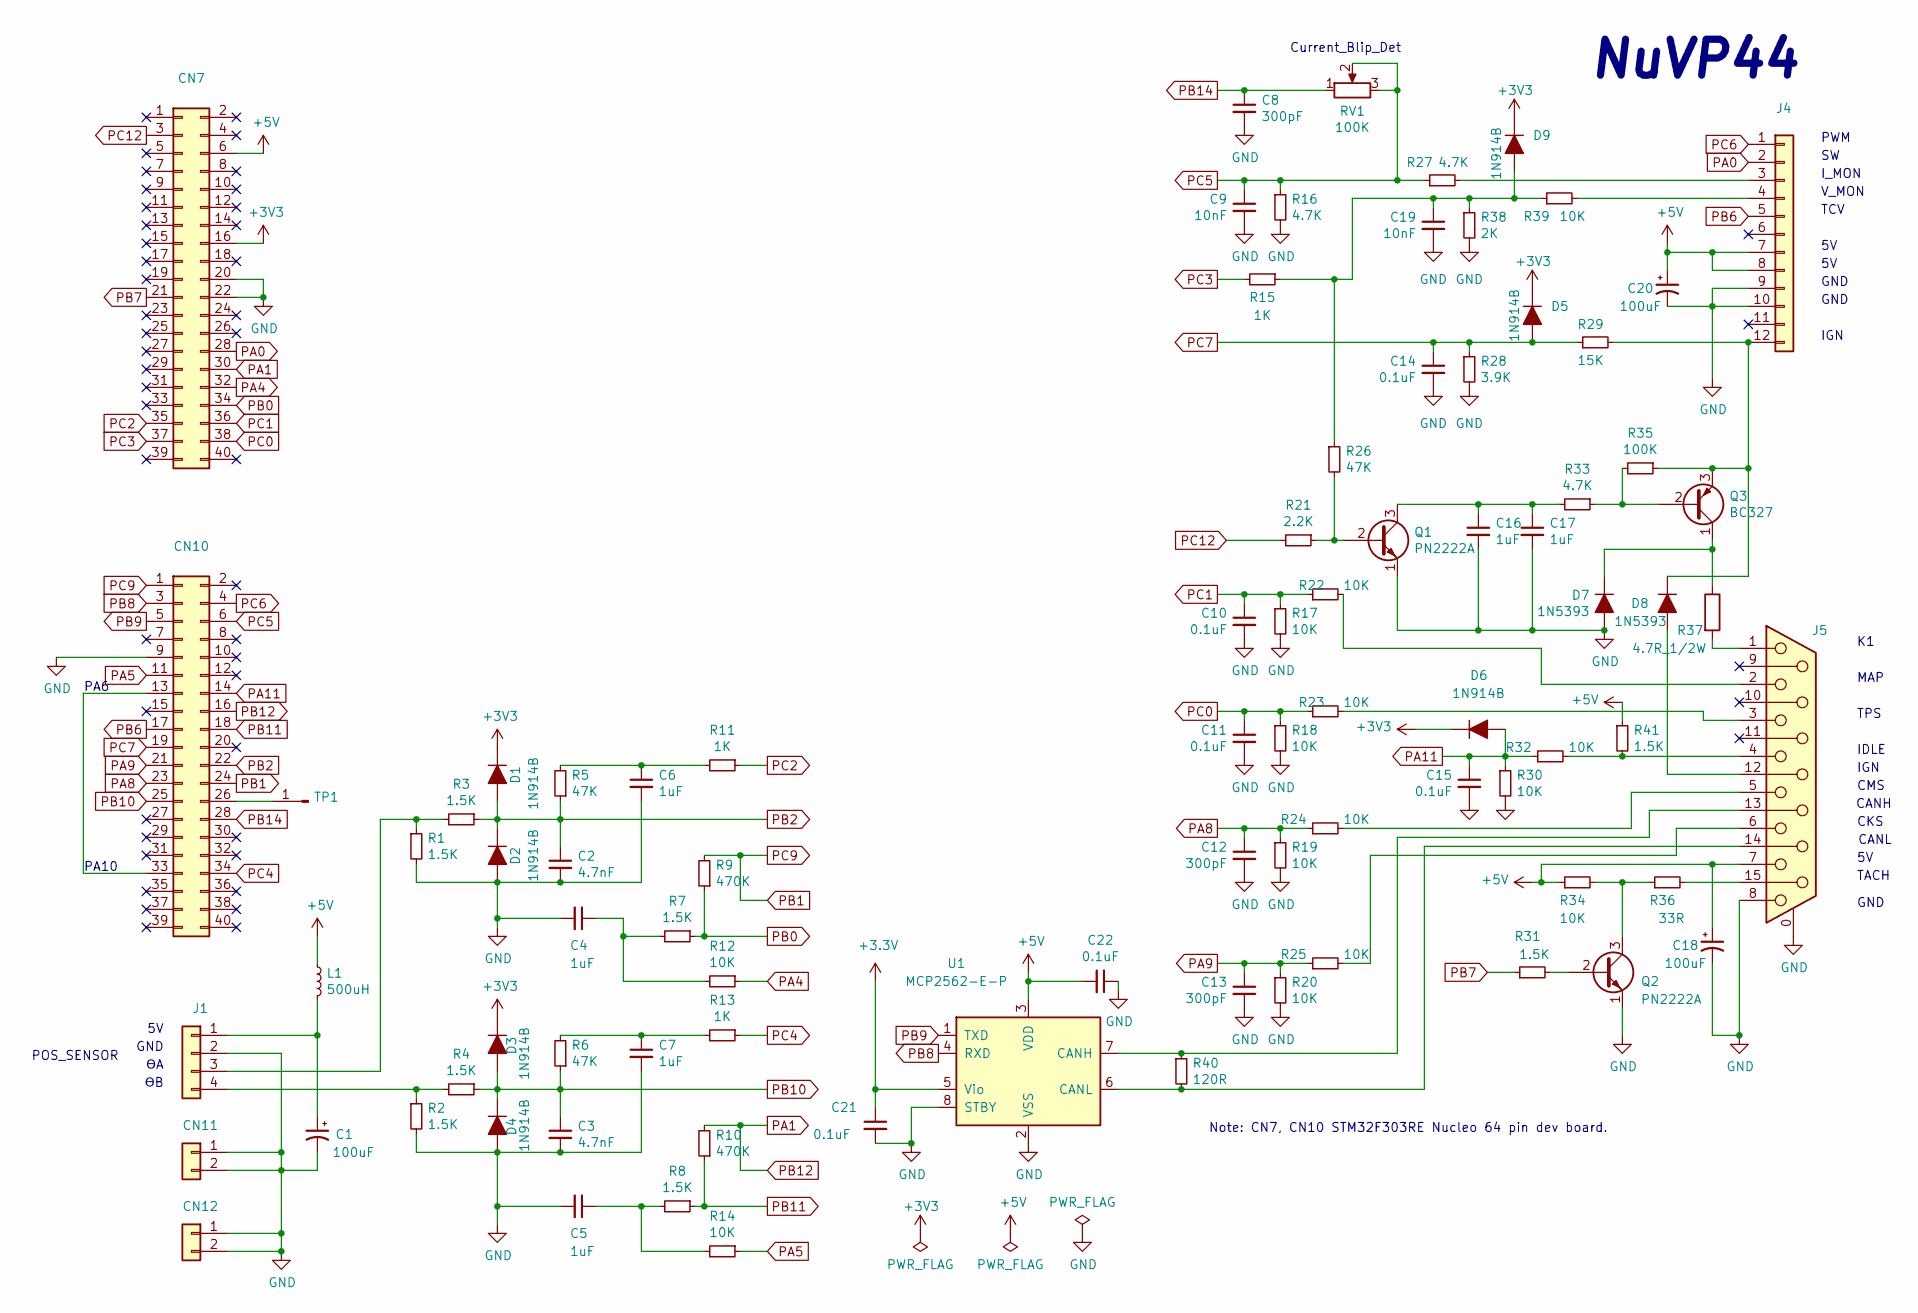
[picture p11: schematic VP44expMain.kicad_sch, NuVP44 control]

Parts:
C1, C18, C20: 100uF; CP_Radial_D5.0mm_P2.50mm
C2, C3: 4.7nF; C_Disc_D5.0mm_W2.5mm_P5.00mm
C4, C5, C6, C7, C16, C17: 1uF; C_Disc_D5.1mm_W3.2mm_P5.00mm
C8, C12, C13: 300pF; C_Disc_D5.0mm_W2.5mm_P5.00mm
C9, C19: 10nF; C_Disc_D5.0mm_W2.5mm_P5.00mm
C10, C11, C14, C15, C21, C22: 0.1uF; C_Disc_D5.0mm_W2.5mm_P5.00mm
CN7, CN10: Conn_02x20_Odd_Even; PinHeader_2x20_P2.54mm_Vertical
CN11, CN12: Conn_01x02_Female; PinHeader_1x02_P2.54mm_Vertical
D1, D2, D3, D4, D5, D6, D9: 1N914B; D_DO-35_SOD27_P7.62mm_Horizontal
D7, D8: 1N5393; D_DO-41_SOD81_P12.70mm_Horizontal
J1: Conn_01x04_Shielded; PinHeader_1x04_P2.54mm_Vertical
J4: Conn_01x12; PinHeader_1x12_P2.54mm_Vertical
J5: DSUB-15_Female_Horizontal_P2.77x2.84mm_EdgePinOffset4.94mm_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
L1: 500uH; L_Axial_L11.0mm_D4.5mm_P5.08mm_Vertical_Fastron_MECC
Q1, Q2: PN2222A; TO-92_Inline
Q3: BC327; TO-92_Inline
R1, R2, R3, R4, R7, R8, R31, R41: 1.5K; R_Axial_DIN0204_L3.6mm_D1.6mm_P7.62mm_Horizontal
R5, R6, R26: 47K; R_Axial_DIN0204_L3.6mm_D1.6mm_P7.62mm_Horizontal
R9, R10: 470K; R_Axial_DIN0204_L3.6mm_D1.6mm_P7.62mm_Horizontal
R11, R13, R15: 1K; R_Axial_DIN0204_L3.6mm_D1.6mm_P7.62mm_Horizontal
R12, R14, R17, R18, R19, R20, R22, R23, R24, R25, R30, R32, R34, R39: 10K; R_Axial_DIN0204_L3.6mm_D1.6mm_P7.62mm_Horizontal
R16, R27, R33: 4.7K; R_Axial_DIN0204_L3.6mm_D1.6mm_P7.62mm_Horizontal
R21: 2.2K; R_Axial_DIN0204_L3.6mm_D1.6mm_P7.62mm_Horizontal
R28: 3.9K; R_Axial_DIN0204_L3.6mm_D1.6mm_P7.62mm_Horizontal
R29: 15K; R_Axial_DIN0204_L3.6mm_D1.6mm_P7.62mm_Horizontal
R35: 100K; R_Axial_DIN0204_L3.6mm_D1.6mm_P7.62mm_Horizontal
R36: 33R; R_Axial_DIN0204_L3.6mm_D1.6mm_P7.62mm_Horizontal
R37: 4.7R_1/2W; R_Axial_DIN0309_L9.0mm_D3.2mm_P15.24mm_Horizontal
R38: 2K; R_Axial_DIN0204_L3.6mm_D1.6mm_P7.62mm_Horizontal
R40: 120R; R_Axial_DIN0204_L3.6mm_D1.6mm_P7.62mm_Horizontal
RV1: 100K; Potentiometer_Bourns_3296W_Vertical
TP1: Conn_01x01_Male; PinHeader_1x01_P2.54mm_Vertical
U1: MCP2562-E-P; DIP-8_W7.62mm_Socket

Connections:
+5V: C18.1, C20.1, C22.2, CN7.6, J4.7, J4.8, J5.7, L1.1, R34.1, R41.1, U1.3 (VDD)
GND: C1.2, C2.2, C3.2, C4.2, C5.2, C6.2, C7.2, C8.2, C9.2, C10.2, C11.2, C12.2, C13.2, C14.2, C15.2, C16.2, C17.2, C18.2, C19.2, C20.2, C21.2, C22.1, CN7.20, CN7.22, CN10.9, CN11.1, CN11.2, CN12.1, CN12.2, D2.2 (A), D4.2 (A), D7.2 (A), J1.2, J4.9, J4.10, J5.0 (PAD), J5.8, Q1.1 (E), Q2.1 (E), R1.2, R2.2, R16.2, R17.2, R18.2, R19.2, R20.2, R28.2, R30.2, R38.2, U1.2 (VSS), U1.8 (STBY)
unnamed: C4.1, R7.2, R12.2
unnamed: C5.1, R8.2, R14.2
unnamed: C6.1, R5.2, R11.2
unnamed: C7.1, R6.2, R13.2
unnamed: CN10.13, CN10.33
unnamed: CN10.26, TP1.1
unnamed: D7.1 (K), Q3.1 (C), R37.1
unnamed: D8.2 (A), J5.12
unnamed: D8.1 (K), J4.12, Q3.3 (E), R29.2, R35.1
unnamed: C19.1, D9.2 (A), R15.1, R26.1, R38.1, R39.1
unnamed: C1.1, J1.1, L1.2
unnamed: J1.3, R1.1, R3.2
unnamed: J1.4, R2.1, R4.2
unnamed: J4.3, R27.2
unnamed: J4.4, R39.2
unnamed: J5.13, R40.1, U1.7 (CANH)
unnamed: J5.14, R40.2, U1.6 (CANL)
unnamed: J5.15, R36.2
unnamed: J5.1, R37.2
unnamed: J5.2, R22.2
unnamed: J5.3, R23.2
unnamed: J5.4, R32.2, R41.2
unnamed: J5.5, R24.2
unnamed: J5.6, R25.2
unnamed: Q1.2 (B), R21.1, R26.2
unnamed: C16.1, C17.1, Q1.3 (C), R33.2
unnamed: Q2.2 (B), R31.2
unnamed: Q2.3 (C), R34.2, R36.1
unnamed: Q3.2 (B), R33.1, R35.2
PA0: CN7.28, J4.2
PA1: CN7.30, CN10.16, R10.2
PA4: CN7.32, R12.1
PA5: CN10.11, R14.1
PA8: C12.1, CN10.23, R19.1, R24.1
PA9: C13.1, CN10.21, R20.1, R25.1
PA11: C15.1, CN10.14, D6.2 (A), R30.1, R32.1
PB0: CN7.34, R7.1, R9.1
PB1: CN10.1, CN10.24, R9.2
PB2: C2.1, CN10.22, D1.2 (A), D2.1 (K), R3.1, R5.1
PB6: CN10.17, J4.5
PB7: CN7.21, R31.1
PB8: CN10.3, U1.4 (RXD)
PB9: CN10.5, U1.1 (TXD)
PB10: C3.1, CN10.25, D3.2 (A), D4.1 (K), R4.1, R6.1
PB11: CN10.18, R8.1, R10.1
PB14: C8.1, CN10.28, RV1.1
PC0: C11.1, CN7.38, R18.1, R23.1
PC1: C10.1, CN7.36, R17.1, R22.1
PC2: CN7.35, R11.1
PC3: CN7.37, R15.2
PC4: CN10.34, R13.1
PC5: C9.1, CN10.6, R16.1, R27.1, RV1.2, RV1.3
PC6: CN10.4, J4.1
PC7: C14.1, CN10.19, D5.2 (A), R28.1, R29.1
PC12: CN7.3, R21.2

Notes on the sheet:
Note: CN7, CN10 STM32F303RE Nucleo 64 pin dev board.
IGN
GND
I_MON
CANL
PA10
NuVP44
Current_Blip_Det
PA6
CMS
TCV
TACH
V_MON
IDLE
PWM
POS_SENSOR
CKS
TPS
MAP
CANH

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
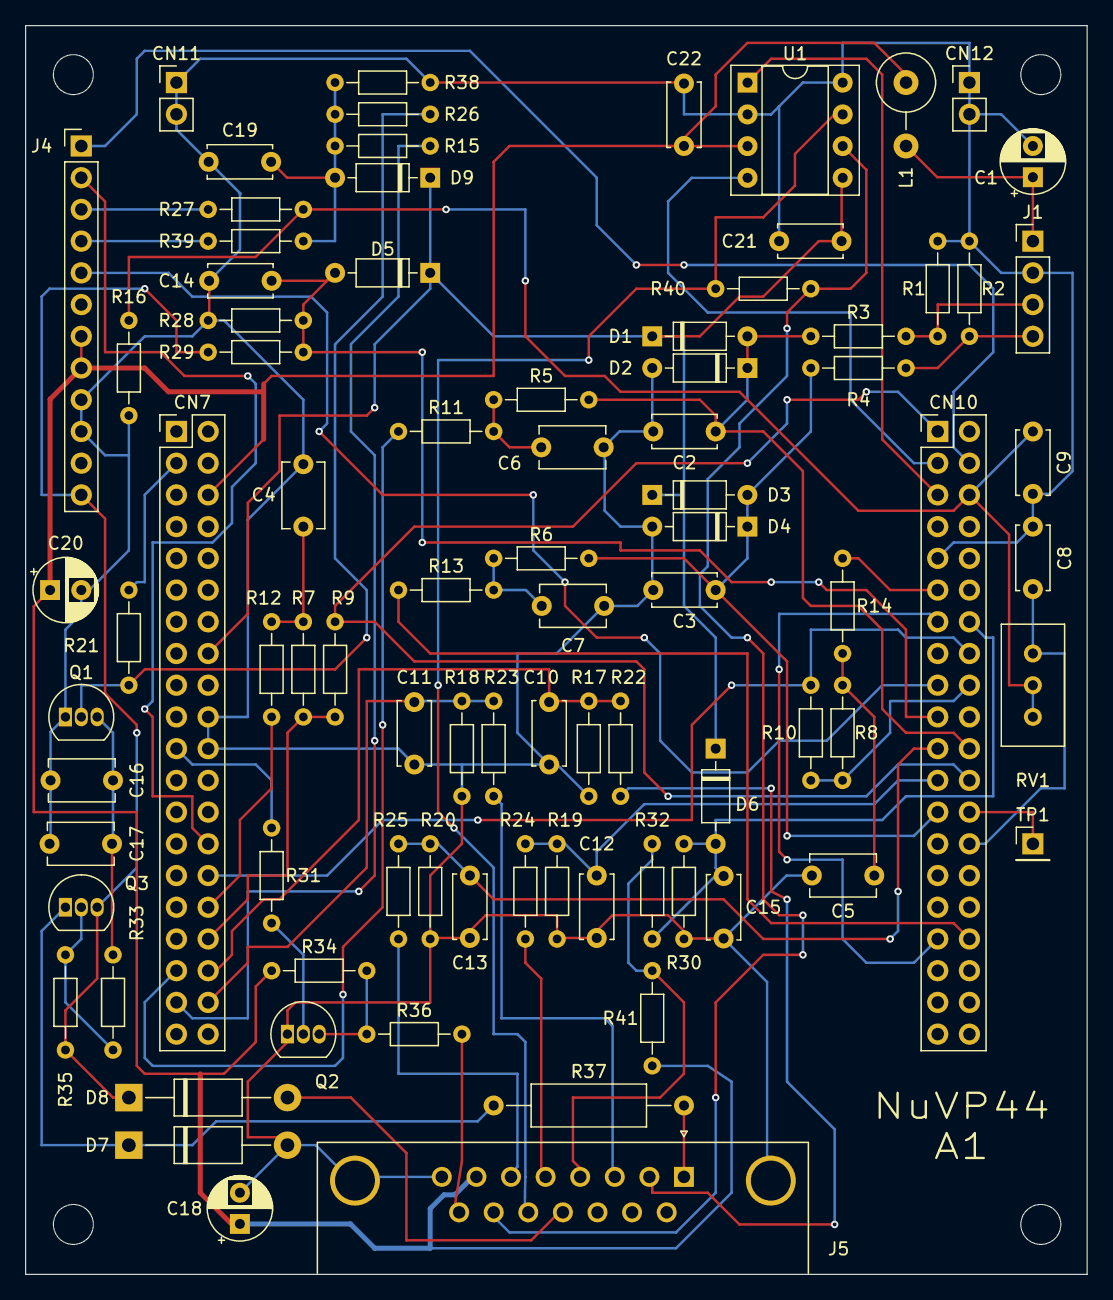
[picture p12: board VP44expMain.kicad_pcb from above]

Board: 2 copper layers, 85.0 x 100.0 mm, 90 parts (0 on the bottom side), 58 nets.

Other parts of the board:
MH1, MH2, MH3, MH4: MountingHole_3.2mm_M3

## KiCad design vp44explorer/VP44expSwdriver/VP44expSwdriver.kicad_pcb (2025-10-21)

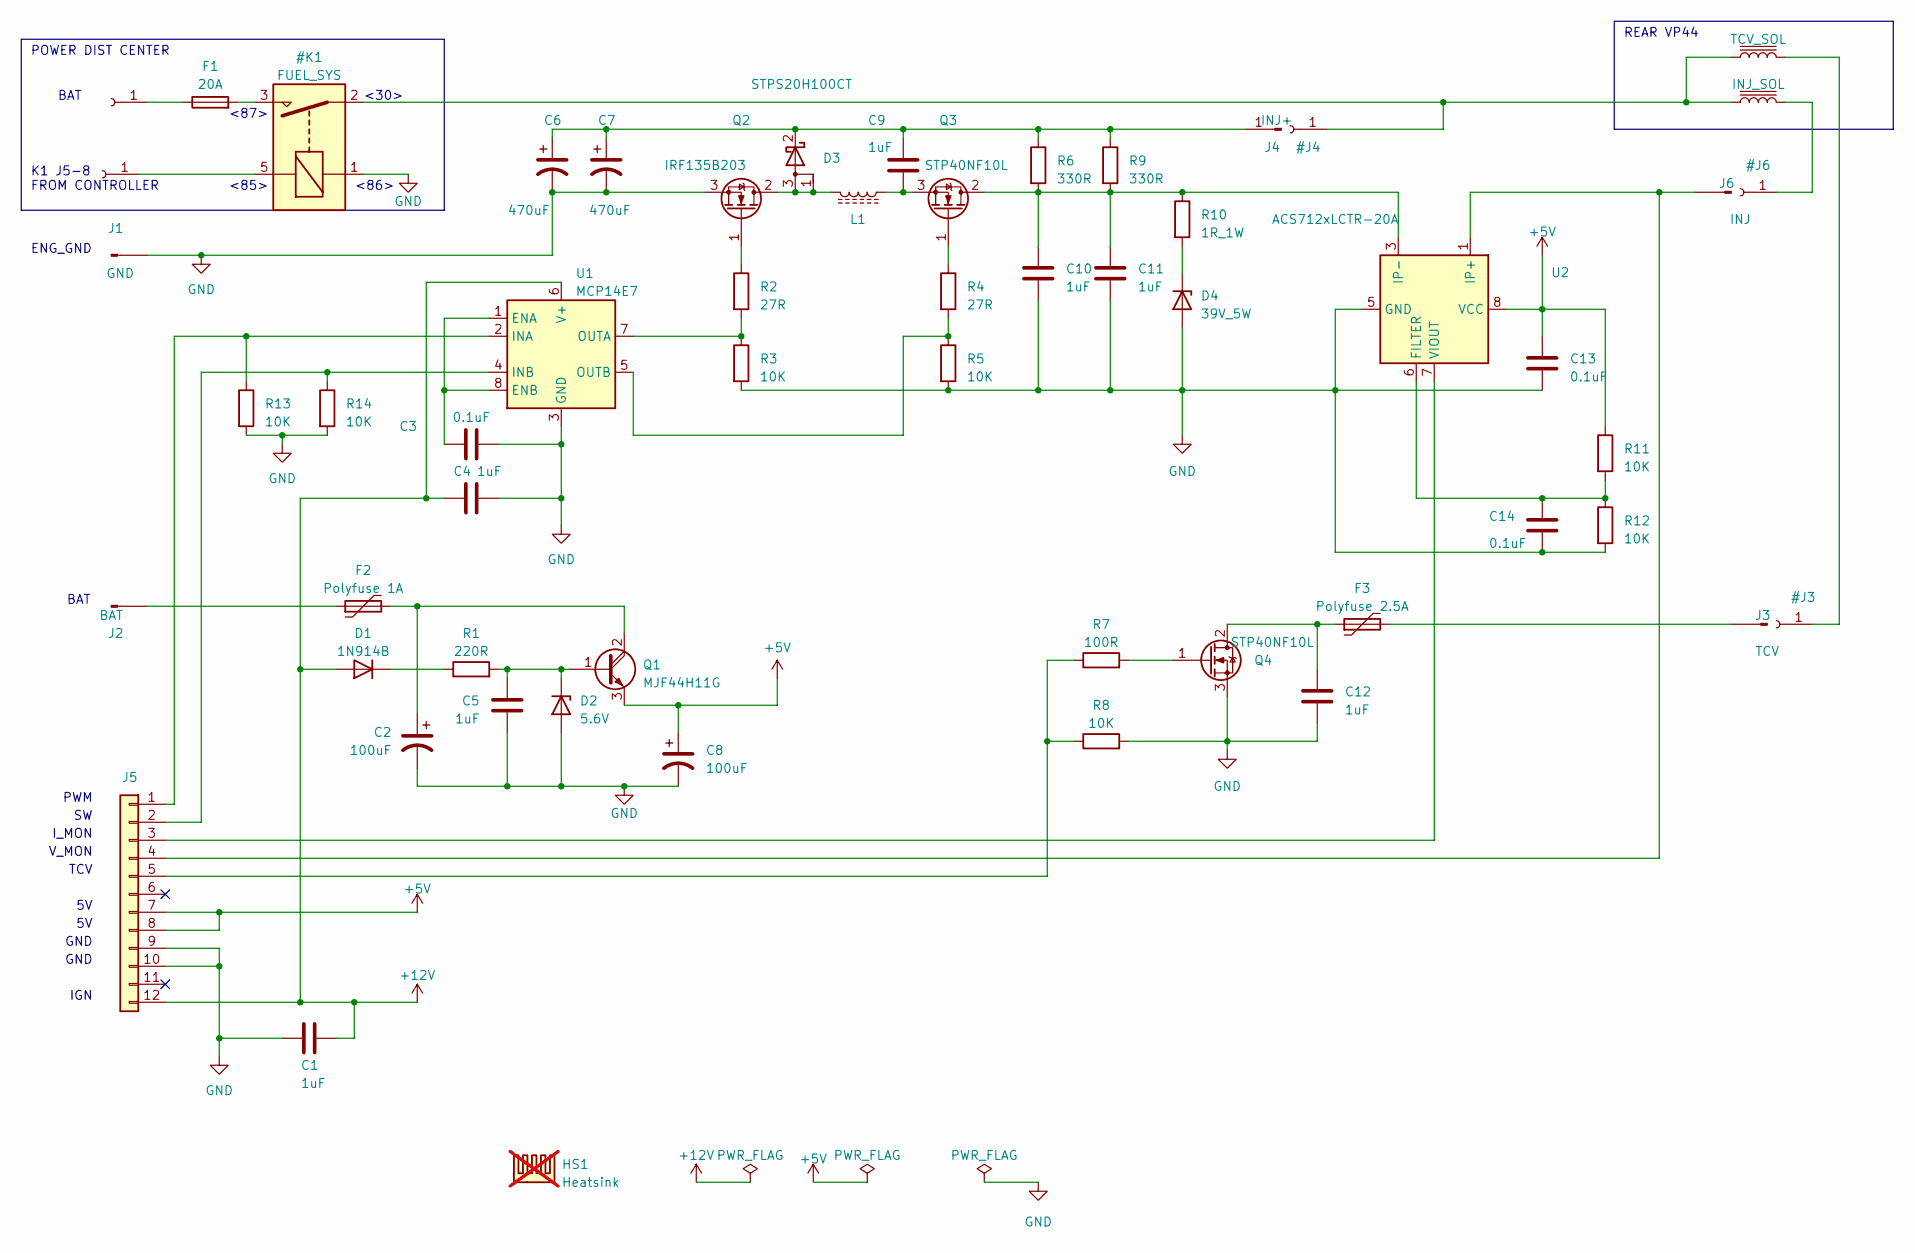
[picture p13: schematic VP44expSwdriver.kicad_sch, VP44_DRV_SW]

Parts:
C1, C4, C5: 1uF; C_Disc_D5.1mm_W3.2mm_P5.00mm
C2, C8: 100uF; CP_Radial_D5.0mm_P2.50mm
C3, C13, C14: 0.1uF; C_Disc_D5.0mm_W2.5mm_P5.00mm
C6, C7: 470uF; CP_Radial_D8.0mm_P5.00mm
C9, C10, C11, C12: 1uF; C_Rect_L16.5mm_W7.0mm_P15.00mm_MKT
D1: 1N914B; D_DO-35_SOD27_P7.62mm_Horizontal
D2: 5.6V; D_DO-41_SOD81_P10.16mm_Horizontal
D3: STPS20H100CT; TO-220-3_Vertical
D4: 39V_5W; D_DO-201AD_P15.24mm_Horizontal
F1: 20A; Automotive ATC
F2: Polyfuse 1A; C_Disc_D8.0mm_W2.5mm_P5.00mm
F3: Polyfuse 2.5A; C_Disc_D8.0mm_W2.5mm_P5.00mm
HS1: Heatsink; 100 X 40 X20 AMAZON.COM; not fitted
J1: GND; SolderWire-2sqmm_1x01_D2mm_OD3.9mm
J2: BAT; SolderWire-2sqmm_1x01_D2mm_OD3.9mm
J3: TCV; SolderWire-2sqmm_1x01_D2mm_OD3.9mm
J4: INJ+; SolderWire-2sqmm_1x01_D2mm_OD3.9mm
J5: Conn_01x12; PinHeader_1x12_P2.54mm_Vertical
J6: INJ; SolderWire-2sqmm_1x01_D2mm_OD3.9mm
L1: L_Ferrite; L_Toroid_Vertical_L26.7mm_W14.0mm_P10.16mm_Pulse_D
L2: TCV_SOL
L3: INJ_SOL
Q1: MJF44H11G; TO-220-3_Vertical
Q2: IRF135B203; TO-220-3_Vertical
Q3, Q4: STP40NF10L; TO-220-3_Vertical
R1: 220R; R_Axial_DIN0309_L9.0mm_D3.2mm_P15.24mm_Horizontal
R2, R4: 27R; R_Axial_DIN0204_L3.6mm_D1.6mm_P7.62mm_Horizontal
R3, R5, R8, R11, R12, R13, R14: 10K; R_Axial_DIN0204_L3.6mm_D1.6mm_P7.62mm_Horizontal
R6, R9: 330R; R_Axial_DIN0309_L9.0mm_D3.2mm_P15.24mm_Horizontal
R7: 100R; R_Axial_DIN0204_L3.6mm_D1.6mm_P7.62mm_Horizontal
R10: 1R_1W; R_Axial_DIN0414_L11.9mm_D4.5mm_P20.32mm_Horizontal
U1: MCP14E7; DIP-8_W7.62mm
U2: ACS712xLCTR-20A; SOIC-8_3.9x4.9mm_P1.27mm

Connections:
+5V: C8.1, C13.1, J5.7, J5.8, Q1.3 (E), R11.1, U2.8 (VCC)
+12V: C1.2, C4.1, D1.2 (A), J5.12, U1.6 (V+)
GND: C1.1, C2.2, C3.1, C4.2, C5.1, C6.2, C7.2, C8.2, C10.2, C11.2, C12.1, C13.2, C14.2, D2.2 (A), D4.2 (A), F1.1, F1.2, J1.1, J5.9, J5.10, L2.1, L2.2, L3.1, L3.2, Q2.3 (S), Q4.3 (S), R3.2, R5.2, R8.2, R12.2, R13.2, R14.2, U1.3 (GND), U2.5 (GND)
unnamed: D1.1 (K), R1.1
unnamed: C5.2, D2.1 (K), Q1.1 (B), R1.2
unnamed: C6.1, C7.1, C9.2, D3.2 (K), J4.1, R6.1, R9.1
unnamed: D4.1 (K), R10.2
unnamed: F2.1, J2.1
unnamed: F3.2, J3.1
unnamed: J5.1, R13.1, U1.2 (INA)
unnamed: J5.2, R14.1, U1.4 (INB)
unnamed: J5.3, U2.7 (VIOUT)
unnamed: J5.4, J6.1, U2.1 (IP+), U2.2 (IP+)
unnamed: J5.5, R7.1, R8.1
unnamed: C2.1, F2.2, Q1.2 (C)
unnamed: D3.1 (A), D3.3 (A), L1.2, Q2.2 (D)
unnamed: Q2.1 (G), R2.1
unnamed: C10.1, C11.1, Q3.2 (D), R6.2, R9.2, R10.1, U2.3 (IP-), U2.4 (IP-)
unnamed: Q3.1 (G), R4.1
unnamed: C9.1, L1.1, Q3.3 (S)
unnamed: C12.2, F3.1, Q4.2 (D)
unnamed: Q4.1 (G), R7.2
unnamed: C3.2, U1.1 (ENA), U1.8 (ENB)
unnamed: R2.2, R3.1, U1.7 (OUTA)
unnamed: R4.2, R5.1, U1.5 (OUTB)
unnamed: C14.1, R11.2, R12.1, U2.6 (FILTER)

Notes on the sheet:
POWER DIST CENTER
I_MON
TCV
IGN
V_MON
ENG_GND
K1 J5-8 FROM CONTROLLER
<86>
<85>
BAT
GND
REAR VP44
<87>
<30>
PWM

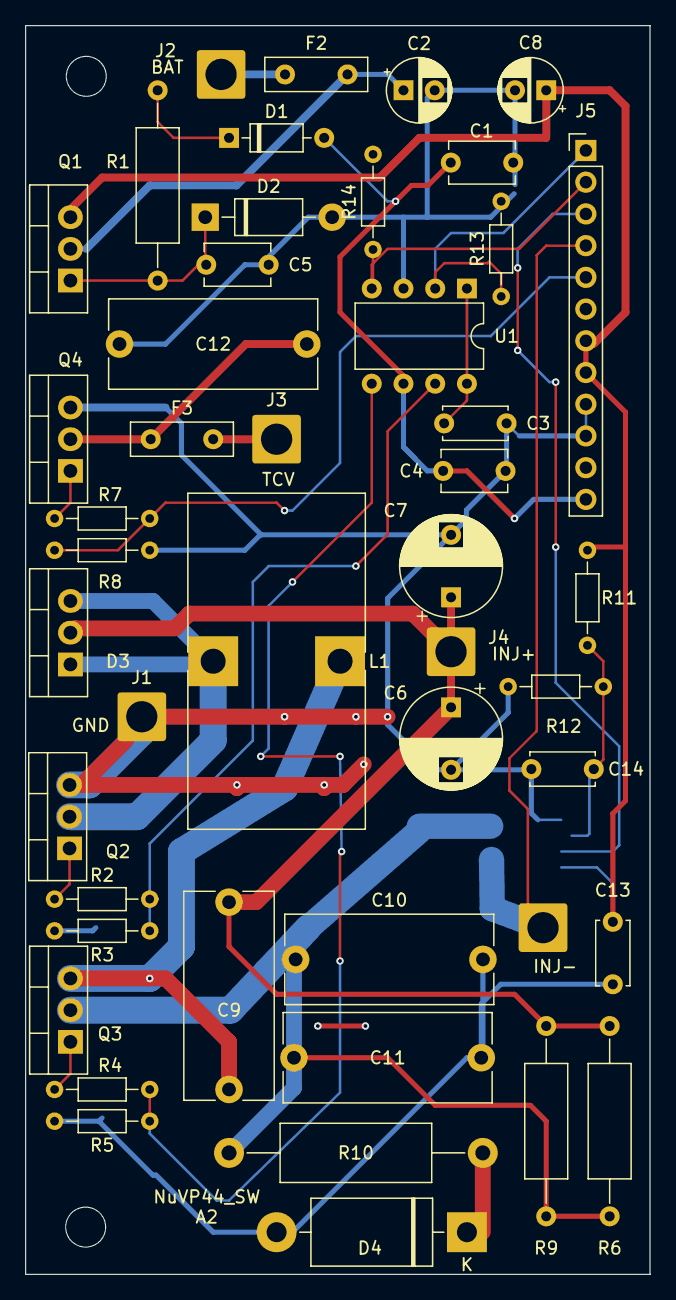
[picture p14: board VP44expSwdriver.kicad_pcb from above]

Board: 2 copper layers, 50.0 x 100.0 mm, 49 parts (1 on the bottom side), 26 nets.

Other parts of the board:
MH1, MH2: MountingHole_3.2mm_M3

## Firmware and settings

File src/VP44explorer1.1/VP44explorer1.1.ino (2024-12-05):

#include <EEPROM.h>
#include <IWatchdog.h>
#include "VP44tables.h"

/*
  VP44 explorer
  ver 1.1
  by Ray Malcuit
  Dec. 2024
  pump controller. Predict SOI time by kinematics -> pump shaft velocity, acceleration method
  arm core nucleo 64 pin STM32f303RE board
  requires STM32duino core, NOT Maple core. Not for cube or HAL.
  higher resolution timer 2 is now 0.5 microsecond per tick.
  Sensors ADC now with DMA, less CPU overhead
  Phase A captured by Timer 8 now.
  Diagnostic trouble codes added
  Internal watchdog timer added
  DTC stored
  Added keyed igniton shutdown and save.
  Rapid injection amps adjustment based on battery voltage.
  Inj sol deadtime based on self induced voltage
  Limp home added
  Injection line delay correction added
  improved idle speed governor with variable kp gain based on load
  works in drive and neutral better. less jumps with AC clutch.
  Added EEPROM storage and defaults for first time use
  Added a cylinder de-activation test.
  moved look-up tables and default params. to VP44tables.h and VP44tables.cpp
  fixed help menu
  added SOE and EOE, cleaned up timer compare register loading. 
  expanded timer 2 and edge counters for future 4 cylinder.

   Pin assignments
   PA0 inj drive out timer2
   PA1 phase B trigger in
   PA2 USART2 TX to ST-link serial to USB converter
   PA3 USART2 RX ^
   PA6 OPAMP2 out inj. sol. monitor blip
   PA8 Cam position sensor, early 24 valve engines
   PA9 Crankshaft position sensor into timer2 ,early 24 valve engines
   PA10 solenoid current capture into timer2 ch 4 from OPAMP2 out
   PA11 idle validation in IDLE = 5V, pedal pressed = 0V
   PB0 OPAMP3 + in adaptive threshold from PC6
   PB1 OPAMP3 out wired to PC9 Testpoint 2
   PB2 OPAMP3 - in phase A from speed sensor
   PB6 timing control valve drive out (PWM)
   PB7 Tachometer square wave out RPM * 2 to PCM
   PB10 OPAMP4 - in: phase B from speed sensor
   PB11 OPAMP4 + in: adaptive threshold from PC8
   PB12 OPAMP4 out wired to PA1 Testpoint1
   PB13 inj solenoid drive current to ADC3 ch5 in
   PB14 Injection solenoid monitor OPAMP2 +in
   PB15 O'scope debug out
   PC0 TPS
   PC1 MAP
   PC2 Phase A ADC in
   PC3 Injection solenoid -
   PC4 Phase B ADC in
   PC5 OPAMP2 - in blip detector and ADC2 ch 11 current in
   PC6 PWM sol drive
   PC7 Ignition on sens
   PC8 spare
   PC9 Phase A trigger in
   PC10 USART3 TX to CCD bus future use
   PC11 USART3 RX to CCD bus future use
   PC12 Fuel system relay drive
*/

#define ON 0X3110;                         //Timer 2 compare Ch. 1 register pin states on match high
#define OFF 0X3120;                        // TIM2->CCMR1 = off, pin goes low when match occurs...
#define NO_CHANGE 0X3100;                  //cause interrupt only pin remains the same
#define FORCE_LOW 0x3140;                  //forces tim2 ch1 pin low
#define _50HZ 1440;                        //TIM16 prescaler
#define _60HZ 1200;                        //
#define scopeLow GPIOB->BRR = 0X8000;      // PB15 off - fast method O-scope goes low
#define scopeHigh GPIOB->BSRR = 0X8000;    //PB15 sync to O-scope goes high
#define scopeToggle GPIOB->ODR ^= 0X8000;  //PB15 sync to O-scope toggle
#define TACHhigh GPIOB->BSRR = 0X0080;     //Tach signal output PB7 high inverted at connector;
#define TACHlow GPIOB->BRR = 0X0080;       // PB7 Tach signal low - inverted at conn;

volatile uint32_t phaseA[60];
volatile uint32_t phaseB[60], phaseBpredict[60];
volatile uint32_t BLIPtime[10], TrefTime;
volatile uint32_t lastA, lastB;
volatile int cycle, oldCycle, okToInj, injMalfunction;
volatile int phaseA_edge, phaseB_edge, old_phaseB_edge, CKPsync, CamSync, CKP_cnt1, BLIPcnt;
volatile uint32_t velocity, SOE, SOI, EOI; 
volatile int32_t EOE;
volatile uint16_t velocityA, oldVelocityA;
volatile int16_t accelA;
volatile int accel, event, predictErr, VPsync, timeout;
uint16_t timingDuty, RecTimingDuty;
int32_t AmpErr;
int TrefEdge, deadTime1Bat, DTC, storedDTC, TimingRetrys;
int TCerror, lastTC, TimError, active_cyl, kill = 0;
int TPS, MAP, SOL, idle_valid, crank = 2;
int RPM, RPMavg, printPauseT;
float Timing, Timing2, oldTiming, desiredTim, desiredTimNL, desiredTimFL, TerrorP, amps, amps1;
float TPSv, MAPv, BATv, AMPS, ampErr, Load;
float milliLiters;
uint16_t AD2result[6], AD1result[6];  //ADC2 global var
int help;
int amps_ref1;
int amps_ref2;
int amps_hold1;
int amps_hold2;
int duty4AutoAdj;
uint16_t RevCounter, checksum;
bool Limp, WasIWDreset, Amps_Reduced;
int RpmFuelLimit = 4095, MapFuelLimit = 4095, BOOST;
int fuelGov2 = 2000;
int TempInt, coldStart, offset = 300;
uint TPS_scaled;
uint32_t printInterval = 500;

/****** Get the factory calibration values from system memory to improve the internal temperature sensor accuracy****/
uint32_t VREF_INTERNAL = 0x1FFFF7BA;
uint16_t Vrefi = *((uint32_t *)(VREF_INTERNAL));
uint32_t TEMP30 = 0X1FFFF7B8;
uint16_t temp30 = *((uint32_t *)(TEMP30));
uint32_t TEMP110 = 0x1FFFF7C2;
uint16_t temp110 = *((uint32_t *)(TEMP110));
float TS = 1710;

//Firimg order
const int FiringOrd[]{ 0, 1, 5, 3, 6, 2, 4 };   //4 cyl 0, 1, 3, 4, 2

const uint8_t
  phaseB_in = PA1,
  CMP = PA8,
  idle = PA11,
  phaseA_in = PB3,
  TACH = PB7,
  O_scope = PB15,
  IGN = PC7,
  failsafe = PC12,
  button = PC13;

void setup() {
  // Arduino core may set these registers as needed, But also added here for some possible low level uses.
  RCC->AHBENR |= 0x300E0003;  //Clock enable ADC 1,2,3,4 GPIO ports A,B,C and DMA1,2
  //RCC->APB1ENR |= 0x24000007;   //Turn on some clocks, DAC1,2 Timer 2,3,4 enabled
  RCC->APB1ENR |= 0x26000007;  //Turn on some clocks, DAC1,2 Timer 2,3,4 enabled   *** CAN enabled
  RCC->APB2ENR |= 0x00027001;  //Clock enable, Tim8, Tim16, SPI1, USART1, SYSCFGEN (required by COMP)

  if (IWatchdog.isReset()) {
    WasIWDreset = 1;         //was it a POR or watchdog reset, used for Diagnostics
    IWatchdog.clearReset();  //clear the reset flag
  }
  IWatchdog.begin(2000000);  //internal watchdog resets CPU after 2 second if execution freezes or go off track

  Serial.begin(115200);  //start serial PA2 TX. PA3 RX. to st-Link which is USB converter
  delay(100);            //let USB get going

  if (WasIWDreset) {
    //Serial.println(" DTC P1688 ");  //internal fuel pump controller failure
  }
  // get data previosly stored in emmulated EEprom (flash last page)
  if (!WasIWDreset) {
    EEPROM_read();
  }

  pinMode(phaseB_in, INPUT);  //b phase in
  pinMode(idle, INPUT);       //idle validation in
  pinMode(CMP, INPUT);        //early 24 valve cam sensor, single notch
  pinMode(phaseA_in, INPUT);  //phase A in
  pinMode(TACH, OUTPUT);      //Tachometer out
  pinMode(O_scope, OUTPUT);   //O'scope debug out
  pinMode(IGN, INPUT);        //Ignition key on sens
  pinMode(failsafe, OUTPUT);  //failsafe relay
  pinMode(button, INPUT);     //user push button sw on nucleo board

  //******** Speed sensor and injection valve events: timer 2 is fixed at 0.5 uS per tick, capture tooth wheel edges on CH 2 ******
  //********** Main Timer 2 setup************
  HardwareTimer *MainTim2 = new HardwareTimer(TIM2);  //this instance is required for attachinterrupt and ISR handler to work-
  //could possibly be done with low level - NVIC controller
  // Timer 2 is 32 bits wide but has no default pins so pins have to be remapped as ALT FUNC.
  // Timer 2 see datasheet table 14
  GPIOA->AFR[0] |= 0x00000011;  //AF1; PA0 Timer 2 ch 1, PA1 ch 2
  GPIOA->AFR[1] |= 0x00000AA0;  //AF10; PA9 Timer 2 ch 3, PA10 ch 4
  GPIOA->MODER |= 0x00280F0A;   //PA0, PA1 and PA9, PA10 pins set mode alt function.

  TIM2->CR1 = 0X0004;  //INTERNAL CLK, UPCOUNTER, UEV INTERRUPT ENABLED
  TIM2->PSC = 35;      //0.5 micro sec per tick
  TIM2->ARR = 600000;  //300 mS overflows below 90 RPM
  TIM2->CNT = 0;
  TIM2->CCER = 0;        //some timer registers are only writeable when this is disabled
  TIM2->CCMR1 = 0x3130;  //T2C1 force comp out low. T2C2 input capture. WAS 40
  TIM2->CCMR2 = 0X3131;  //input capture ch 3 N8 filter , ch 4 capture
  //the two previous steps have to be done before enabling the channels in the next register below
  TIM2->CCER = 0X3BB1;  // ch1 output compare to pin PA0, ch2 either edge, ch4 capture - edge, ch3 capture any edge was13B1
  TIM2->CCR1 = 600001;  //COMPARE TIMER TO 600001 micro seconds un-reachable

  //****** timer2 interrupts enable *********
  MainTim2->attachInterrupt(T2_OVF);        //Tim2 timeout 300 mS. about 90 RPM
  MainTim2->attachInterrupt(1, T2C1_comp);  //Solenoid driver pin PA0
  MainTim2->attachInterrupt(2, T2C2_capt);  //VP speed sensor phase B
  MainTim2->attachInterrupt(3, T2C3_capt);  //Crank Pos sensor capture PA9
  MainTim2->attachInterrupt(4, T2C4_capt);  //solenoid current 'BLIP' detector

  //*******start timer 2 **********
  TIM2->CR1 |= 0X0001;  //start TIMER2

  //******** Speed sensor phase A timer 8 is fixed at 0.5 uS per tick, capture tooth wheel edges on CH 4 ******
  //********** Main Timer 8 setup************
  HardwareTimer *MainTim8 = new HardwareTimer(TIM8);  //this instance is required for attachinterrupt and ISR handler to work-
  // Timer 8 is 16 bits wide but has no default pins so pins have to be remapped as ALT FUNC.
  // Timer 8 see datasheet table 14
  GPIOC->AFR[1] |= 0x00000040;  //AF4; PC9 Timer 8 ch 4
  GPIOC->MODER |= 0x00080000;   //PC9 pin set mode alt function.

  TIM8->CR1 = 0X0004;    //INTERNAL CLK, UPCOUNTER, UEV INTERRUPT ENABLED
  TIM8->PSC = 35;        //0.5 micro sec per tick
  TIM8->ARR = 65535;     //16 bits 2^16 - 1
  TIM8->CCER = 0;        //some timer registers are only writeable when this is disabled
  TIM8->CCMR1 = 0x0000;  //T2C1 force comp out low. T2C2 input capture. WAS 40
  TIM8->CCMR2 = 0X3100;  // ch 4 capture N8
  //the two previous steps have to be done before enabling the channels in the next register below
  TIM8->CCER = 0XB000;  // ch1 output compare to pin PA0, ch2 either edge, ch4 capture any edge, ch3 capture any edge was13B1
  TIM8->BDTR = 0x8000;  //Timer 8 is more advanced, requires MOE master output enable set.

  //****** timer8 interrupts enable *********
  MainTim8->attachInterrupt(4, T8C4_capt);  //Phase A trigger capture

  //*******start timer 8 **********
  TIM8->CR1 |= 0X0001;  //start TIMER8

  //***** TIMER 3 SETUP FOR PWM ON CH 1, 3 *********
  //*******controls fuel solenoid current, buck converter
  GPIOC->AFR[0] |= 0x02000000;  //AF2; PC6 mapped to Timer 3 ch 1 compare
  GPIOC->AFR[1] |= 0x00000002;  //AF2; PC8 mapped to Timer 3 ch 3 compare, not used
  GPIOC->MODER |= 0x00022000;   //port pins selected as alternate functions

  TIM3->CR1 = 0X0004;    // INTERNAL CLK, UEV INT ENABLE, UPCOUNT.
  TIM3->PSC = 0;         //prescaler
  TIM3->ARR = 600;       // sets up 120 KHZ PWM
  TIM3->CCMR1 = 0x0060;  // PWM out to ch1
  TIM3->CCMR2 = 0x0060;  // PWM out to ch3
  TIM3->CCER = 0X0101;   // ACTIVE high OUTPUTs ON T3 ch1/ch3 PIN CN10 PC6/PC8 on Nucleo
  TIM3->CCR1 = 200;      //Duty Cycle phase A; just a starting value. Changed later
  TIM3->CCR3 = 200;      //Duty Cycle phase B; just a starting value. Changed later
  TIM3->CR1 |= 0X0001;   //start TIMER3

  //*********** Timer16 setup. PWM channel 1 drives timing piston control valve *****
  //*********** 50 or 60 HZ output mapped to PB6 ************
  //Chanel TIM16_CH1N chosen so PB8 is resevered for CAN_RX future use.
  GPIOB->AFR[0] |= 0x01000000;  //PB6 TIM16 ch1N
  GPIOB->MODER |= 0x00002000;   //PB6 PWM out
  TIM16->CR1 = 0x0004;          // INTERNAL CLK, UEV INT ENABLE, UPCOUNT.
  TIM16->PSC = 1440;            // prescaler 72MHZ / 1440
  TIM16->ARR = 1000;            // sets up 50 60 HZ PWM 100% duty cycle= 1000
  TIM16->CCMR1 = 0x0060;        // PWM out to ch1 PB6
  TIM16->CCER = 0x0004;         // ACTIVE high OUTPUTs
  TIM16->CCR1 = 500;            // DUTY CYCLE, Just a starting value. Changed later
  TIM16->BDTR = 0x8000;         //Timer 16 is more advanced, requires MOE master output enable set.
  TIM16->CR1 |= 0x0001;         // start TIMER16

  //************ Cam position sensor to PA8 setup *******
  attachInterrupt(digitalPinToInterrupt(CMP), Camshaft_handler, CHANGE);

  //********** set up analog systems *******
  ADC1_setup();
  ADC2_setup();
  DAC_set();
  OPAMP2_set();
  OPAMP3_set();
  OPAMP4_set();
  delay(10);  //let the ADCs get some conversions into DMA

  if (AD2result[0] > 750) {  //If solenoid has battery over 3.5V then fuel system relay fault
    //DTC = 1285;              //should not be turned on yet.
    Serial.print(" DTC P");
    Serial.println(DTC);
  }
  //fuel solenoid will be ruined if left on too long. WARNING! do not defeat the failsafe relay funtion.
  pinMode(failsafe, OUTPUT);     // fuel system relay drive also failsafe shutdown incase software or hardware malfunction
  digitalWrite(failsafe, HIGH);  // Turn on fuel system relay
  delay(200);                    // so the relay has time to engage
  pinMode(failsafe, INPUT);      //fuel system relay should latch on by hardware now. goto high Z state

  Serial.println(" Enter ? for help menu ");
  CANsetup();       //config the CAN periph
  if (tempCalcInternal(AD1result[0]) < 60) { coldStart = 1; }

}  //setup done
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
void loop() {
  //call these functions on every phase B tooth edge
  if (phaseB_edge != old_phaseB_edge) {
    old_phaseB_edge = phaseB_edge;
    injManager();  //this fuction computes RPM, and splits up tasks and events
  }

  //call these fuctions on every cylinder injection cycle
  if (cycle != oldCycle) {
    if (cycle > 6) {  //4 cyl>> 4
      cycle = 1;
    }
    oldCycle = cycle;
    active_cyl = FiringOrd[cycle];
    timingControl();  //adjust TCV PWM to achieve desired timing advance
    if (cycle == 1 || cycle == 5) {
      RevCounter++;  //inc every crankshaft revolution 2x camshaft
    }

    Amps_Reduced = 0;
  }

  //call these functions whenever
  threshold();  //samples the phase A, B VP speed sensor and calc the zero cross thresholds
  sanityCheck();
  REC();  //check serial port for incoming
  AmpsReduce();
  //CANrec();
  if (help) {
    Help();
    printInterval = 10000;  //delay the stats and RPM printing so help menu can be read
  }
  printOut();
  ignitionOff();

  //call these functions if engine is stopped
  if (timeout) {
    getSensors();        //convert raw ADC samples to TPS, MAP, etc
    SOL = AD2result[0];  //to calc volts with sol. resting
    SetAmps();           //auto adjust the inj sol. amps
    SetDeadtime2();
    governor();  //not turning, call governor so it updates fuel for starting
    TempInt = tempCalcInternal(AD1result[0]);
  }

  //time interval functions
  //CAN is in loopback mode and not really doing anything.
  static uint32_t lastCAN_send;
  if (millis() - lastCAN_send > 500) {
    lastCAN_send = millis();
    CANsend();
  }

  IWatchdog.reload();  //if stack got here feed the watchdog

}  //Main loop done

void injManager(void)  //******* this executes on every B tooth edge *******
{
  //***** tasks for tooth edges and split up the CPU load *****
  static int lastRPM;
  if (phaseB_edge == 1) {
    amps_ref1 = AD2result[1];
    //deadTime1 = deadTime1 - ((BLIPtime[1] - phaseB[19])/8);
    deadTime1 = constrain(deadTime1, 300, 1000);
  }
  if (phaseB_edge == 3) {  //*** calc RPM ***
    //RPMavg = (RPMavg + (40000000 / phaseB[36])) / 2;
    RPM = 40000000 / phaseB[36];
    RPMavg = lastRPM + ((RPM - lastRPM) / 4);
    RPM = constrain(RPM, 0, 6000);
    RPMavg = constrain(RPMavg, 0, 6000);
    lastRPM = RPM;
    // 4 cyl. use RPM = 60000000 / phaseB[56];
  }
  if (phaseB_edge == 4) {
    timingCompute();
  }
  if (phaseB_edge == 5) {
    amps_ref2 = AD2result[1];
    SOL = (SOL + AD2result[0]) / 2;  //to calc volts with sol. resting
  }
  if (phaseB_edge == 6) {
    SetAmps();
    SetDeadtime2();  //new method
  }
  if (phaseB_edge == 7) {
    governor();
  }
  if (phaseB_edge == 8)  //  calculate the engine load.
  {
    getSensors();
    Load = LoadCalc(fuelGov2);
    MapFuelLimit = MapFuelLookup(BOOST);
  }
  if (phaseB_edge == 21 + crank) {  //4 cyl 31
    amps_hold1 = AD2result[1];
    RpmFuelLimit = RPMFuelLookup(RPMavg);
  }
  if (phaseB_edge == 22 + crank)  //ADC conversion should be done now //4 cyl 32
  {
    amps_hold2 = AD2result[1];
  }
  if (phaseB_edge >= 34) {    // 4 cyl 44
    TIM2->CCMR1 = FORCE_LOW;  //T2C1 force low. never inject past edge 34.
    TempInt = tempCalcInternal(AD1result[0]);
  }

}  //injManage done

void governor(void) {
  /****** Cummins 24V VP44 PID based governor.*******
      notice no dt or time interval. this is called on every injection cycle so dt is speed dependant.
      RPM is measured and calculated on each injection cycle, so there is no sense trying to adjust
      fuel until the RPM change is observed from the last fuel change.
      TPS is 0 - 5 volt sensor with idle saftey switch built in
      It is about .45 v resting and just less then 4 volts WOT.
      TPS output is halfed with 10 Kohm resistors so it wont exceed 3.3 volts limits of STM32F303 chip
  */
  static float fuelGov, lastFuelGov;
  static float lastRPM;
  static int TempComp;
  static int fuelp, fueli, fueld;
  int SetPoint = 800;  //desired idle speed
  //int FuelBias = 1570;  //changed type to global var. typical fuel level to cause idle speed at 800 RPM
  const int MaxFuel = 4095;                  //4095 is the max allowable fueling level. 3600 is stock-ish
  const int SoftRev = 3000, HardRev = 3200;  //Rev limiter
  float kpL = kp / 100.0, kiL = ki / 100.0, kdL = kd / 100.0;
  float LF = Load - 3.0; 
  LF = constrain(Load, 0.0 , 2.0);
  kpL = mapf(LF, 0.0, 2.0, kpL, kpL/5);
  TPS_rest = constrain(TPS_rest, 200, 300);
  TPS_floored = constrain(TPS_floored, 1700, 2300);
  FuelBias = constrain(FuelBias, 1200, 1800);

  if (coldStart) {
    TempComp = 180 - (RevCounter);  //sets fuel bias a bit higher for smoother cold startup
    TempComp = constrain(TempComp, 0, 400);
  }

  TPS_scaled = map(TPS, TPS_rest, TPS_floored, (FuelBias + TempComp), 4095);
  TPS_scaled = constrain(TPS_scaled, FuelBias, 4095);
  SetPoint = SetPoint + (TempComp / 4) + ((TPS_scaled - FuelBias) / 5);  //was 5 determines going off idle feel. 5 is lazier than 4
  fuelp = SetPoint - RPM;
  fuelp = constrain(fuelp, -150, 150);
  fueli = fueli + (fuelp * kiL);
  fueli = constrain(fueli, -250.0, droop);
  fueld = RPM - RPMavg;//lastRPM;
  lastRPM = RPM;
  if (fueli > 20 && RPM > 820) { fueli = fueli / 3; }   //control integral wind-up.
  if (fueli < -20 && RPM < 780) { fueli = fueli / 3; }
  fuelGov = fuelp * kpL + fueli - fueld * kdL;
  fuelGov = constrain(fuelGov, -300.0, droop);
  fuelGov = fuelGov + TPS_scaled;
  //********* Enforce Table limits ******
  //fuel vs RPM
  if (RpmFuelLimit <= MapFuelLimit) {  //enforce the most restrictive results from fuel tables
    //fuelGov = constrain(fuelGov, 0, RpmFuelLimit);  //un-comment to enable table
  }
  //fuel vs BOOST
  else {
    //fuelGov = constrain(fuelGov, 0, MapFuelLimit);  //un-comment to enable table
  }

  //********** Anti stall ****** mostly un-tested need a manual transmission.
  if (RPM < 740) {
    //fuelGov = fuelGov + 50; //quick response
    fuelGov = fuelGov + constrain(((740 - RPM) * 3), 0, 300);  //porpotional response
  }

  //**********starting***********
  if (RPM < 400) {  //retard timing 3 deg
    //crank = 1;        //SOI on B tooth edge 20
    //fuelGov =  2400 + (TPS - RestingPos) / 2;
  }
  if (RPM < 325) {  //retard timing 6 deg and even more fuel
    crank = 2;      //SOI on B tooth edge 21

  } else {
    crank = 0;  //SOI on B tooth edge 19. Normal running
  }

  //*********** Rev limit ******
  if (RPM > SoftRev) {
    fuelGov = fuelGov - (RPM - SoftRev) * 3;  //eg 2950 - 2800 = 150 times 3 = 450 fuel units removed
  }
  if (RPM > HardRev) {
    fuelGov -= 2000;
  }
  //**********Limp home limits **************
  if (Limp) {
    if (RPM > 1700) {
      fuelGov = fuelGov - (RPM - 1700) * 2;
    }
    fuelGov = constrain(fuelGov, 0, FuelBias + 1000);
  }
  //*******idle validation switch check********
  if (RPM > 1300 && idle_valid)  //idle valid switch is 5V at idle. 0V when pedal pushed
  {
    fuelGov = fuelGov - (RPM - 1300) * 2;             //limit RPM  to about 1300
    fuelGov = constrain(fuelGov, 0, FuelBias + 600);  //hard fuel limit
  }
  //********* finalize fuel *********
  fuelGov = (fuelGov + lastFuelGov) / 2.0;  //rolling average fuelGov output for smoother response
  lastFuelGov = fuelGov;

  //*********turn off a cylinder for testing*****
  if (RPM > 600 && kill > 0 && kill == active_cyl) { fuelGov = 0; }
  fuelGov2 = constrain(fuelGov, 0, MaxFuel);  //Atomic fuelGov2 (output) may get destroyed in EOI funtion
  //fuelGov2 = TPS_scaled; //un-comment to disable gov.
}  //govenor done


//******** load calculator **********
//calc the fuel plungers stroke %,  comp for the non linear ramp of the cam donut. Sinusoidal for now.
float LoadCalc(uint32_t fuel) {
  float stroke;
  float _load;
  for (int i; i < 9; i++) {
    if (fuel >= strokeCorrection[i]) {
      stroke = (12.5) * i;
      float r = (fuel - strokeCorrection[i]) / (float)(strokeCorrection[i + 1] - strokeCorrection[i]);
      stroke = (12.5 * r) + stroke;
    }
  }
  //fuel plungers are 7.5 mm dia. x 3.5 mm stroke x 3 plungers. volume 124 ml = 3*((7.5 / 2) * pi * 3.5)
  milliLiters = (124 * stroke) / 100.0;  //injected quanity per cylinder  //Nissan 4 cyl 77 mL ?

  //cam lobe Load correction from above now scaled to 0 every 200 RPM when at no load in neutral
  int l = RPM / 200;  //table entry for every 200 RPM
  l = l - 5;
  l = constrain(l, 0, 20);  //1000 to 4000 RPM
  int base_fuel = BaseFuel[l];
  if (RPM % 200 && l < 20) {  //if odd RPM then split the difference
    base_fuel += (BaseFuel[l + 1] - BaseFuel[l]) / 2;
  }
  _load = mapf(fuel, base_fuel, 4095.0, 0.0, 100.0);
  _load = constrain(_load, 0.0, 100.0);  //used for Timing advance table
  return _load;
}
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

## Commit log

2024-11-01 name
    PCB gerbers
2024-11-01 PCB gerbers
2024-11-14 Create dual in2 .csv
    [dual in2 .csv]
2024-11-24 updated
    Part numbers. fixed missing R13 & R14
    [VP44explorerSWdrv_1_1_BOM.csv]
2025-10-21 KiCad project
    [VP44detail.kicad_pcb, VP44detail.kicad_sch, VP44expLNdriver.csv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]
